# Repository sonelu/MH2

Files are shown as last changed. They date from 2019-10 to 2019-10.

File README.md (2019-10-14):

# MH2

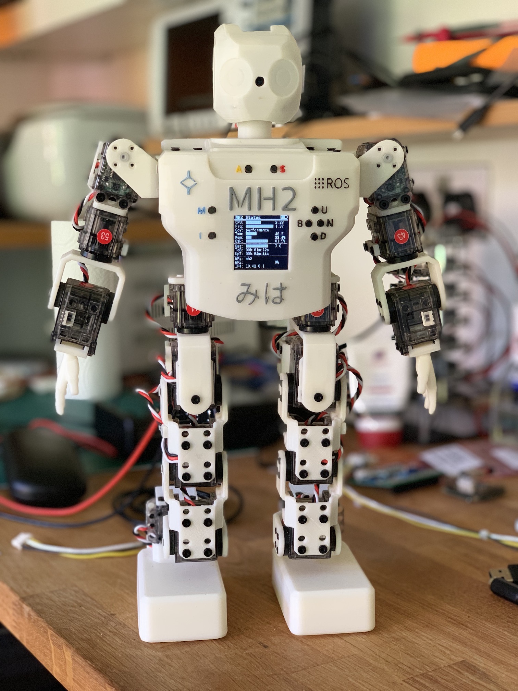
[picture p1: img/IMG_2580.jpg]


Miha 2 (Mini Humanoid Gen 2) is a 22 Degrees of Freedom (DOF) Humanoid Robot intended for research and learning.

The main features of the robot are:

* 22 high performance daisy chained actuators [XL-320](http://emanual.robotis.com/docs/en/dxl/x/xl320/) from Robotis
* Main controller: [FriendlyElec NanoPi Neo Core2 LTS](https://www.friendlyarm.com/index.php?route=product/product&path=69&product_id=211) with:
  - Quad-Core Allwinner H5 processor at 1.5GHz
  - 1GB RAM
  - only 7g weight
* [Custom add-on board](add-on.md) with:
  - 4 channels Dynamixel bus (provided by a [FTDI4232H](https://www.ftdichip.com/Support/Documents/DataSheets/Modules/DS_FT4232H_Mini_Module.pdf) (USB to UART 4 channels)
  - [LSM330](https://media.digikey.com/pdf/Data%20Sheets/ST%20Microelectronics%20PDFS/LSM330.pdf) 6 axis IMU (accelerometer and gyroscope)
  - [Murata 5V 1.5A high performance DC/DC convertor](https://power.murata.com/data/power/oki-78sr.pdf)
* 5MP USB camera (in the head)
* 1.5" 128x128 pixel OLED display (I2C SSD1327 chip)
* 8 tactile switches controlled with a TCA9538 I2C I/O expander providing easy interation with the menues on display
* Power provided by 4 18650 industry standard rechargeable batteries located in the feet and hotswappable; the hotswap capability is provided by a pair of small cicuits that provide a "smart diode" functionality, preventing rush current while chainging the batteries. **A full charge allows aproximatelly 4 hours of operation**.

The [software](./mh2/) is based on the [pypot](https://github.com/poppy-project/pypot) library and I have plans to include ROS support by leveraging the [ROBOTIS-Framework](https://github.com/ROBOTIS-GIT/ROBOTIS-Framework) packages.

The [robot parts](./stl) are 3D printed.

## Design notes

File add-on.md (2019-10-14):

# Add-On Board for MH2

The MH2 robot uses the [FriendlyElec NanoPi Neo Core2 LTS](https://www.friendlyarm.com/index.php?route=product/product&path=69&product_id=211) main controller. To control the Dynamixel servomotors it uses a custom add-on board:

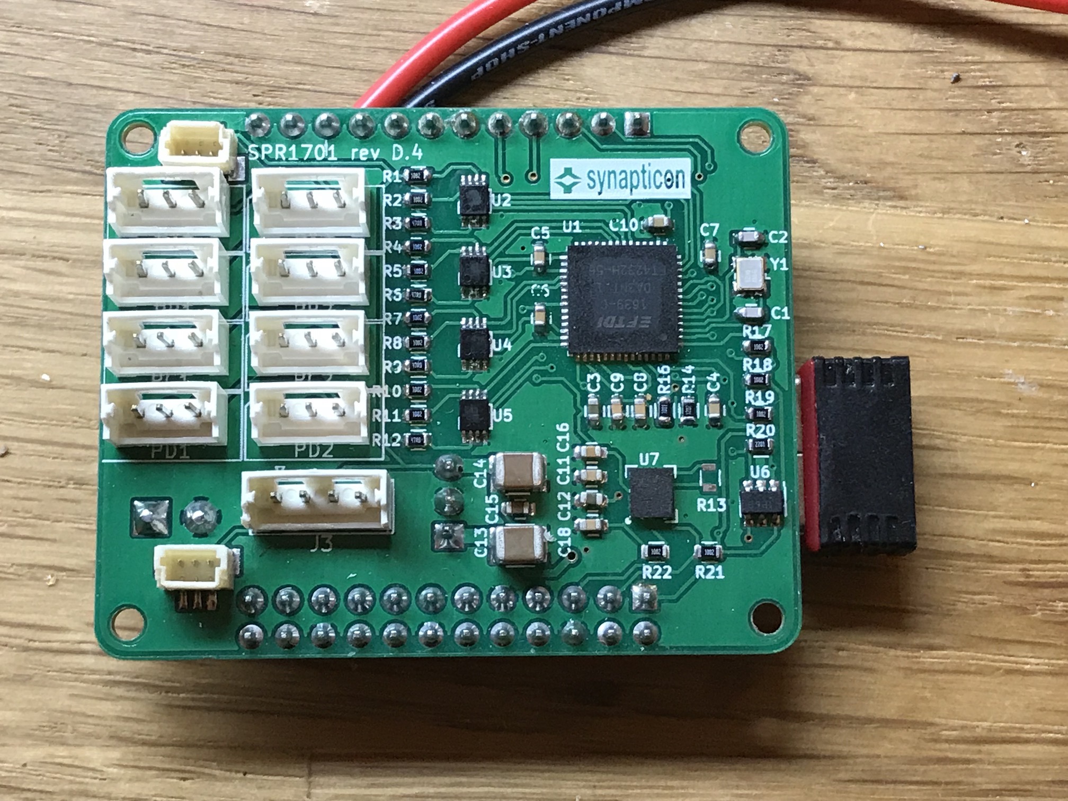
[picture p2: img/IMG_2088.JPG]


This board provides the following:

* uses one of the USB from the NanoPi board and [FTDI4232H](https://www.ftdichip.com/Support/Documents/DataSheets/ICs/DS_FT4232H.pdf) chip to produce 4 UART channels (they will appear as /dev/ttyUSB0 to /dev/ttyUSB3 to the operating system)
* the FTDI chip is programmed using a [93LC46BT](http://www.microchip.com/mymicrochip/filehandler.aspx?ddocname=en550232) 1K EEPROM to configure it in RS485 mode (see page 20 in the FTDI4232 datasheet); this way we can easily convert the RX/TX dignals from the UARTs in a semi-duplex signal required by the Dynamixel bus
* the RX/TX pairs and TXDEN is then passed through a [74LVC2G241](http://www.ti.com/general/docs/suppproductinfo.tsp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) buffer for each of the 4 UARTs, producing the 1 wire [semi-duplex](http://emanual.robotis.com/docs/en/dxl/x/xl320/#communication-circuit) serial signal used by the Dynamixel servos
* there are 8 Dynamixel XL-320 connectors ([Molex 53253-0370](https://www.molex.com/molex/products/datasheet.jsp?part=active/0532530370_PCB_HEADERS.xml)), 2 for each channel
* connected on the I2C there is a [LSM330](https://media.digikey.com/pdf/Data%20Sheets/ST%20Microelectronics%20PDFS/LSM330.pdf) 6 axis IMU (accelerometer and gyroscope) that the robot can use to evaluate the posture
* a 4 pin Molex connector for I2C (used by the OLED screen and the button I/O expander)
* 2 connectors for the cooling fans

On the back side of the board we have:

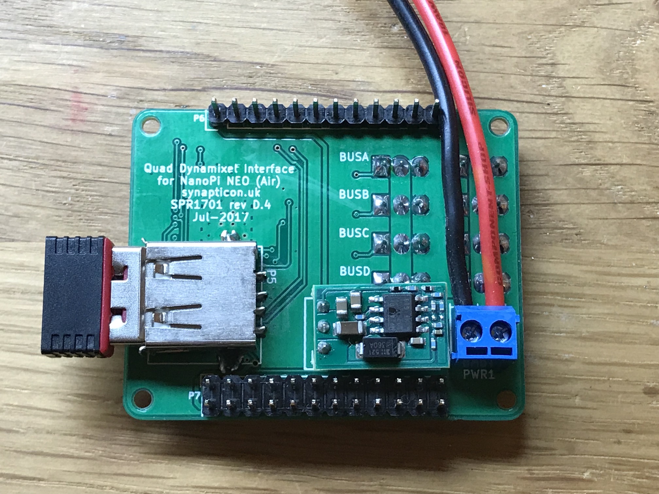
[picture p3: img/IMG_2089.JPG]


* one USB connector for the WiFi dongle (the board does not have WiFi onboard)
* the 5V regulator (1.5A) [Murata OKI-78SR-5/1.5-W36-C](https://power.murata.com/data/power/oki-78sr.pdf)
* the connector the external power jack

The board is fitted directly on top of the GPIO pins of the NanoPi Neo Core2 board:

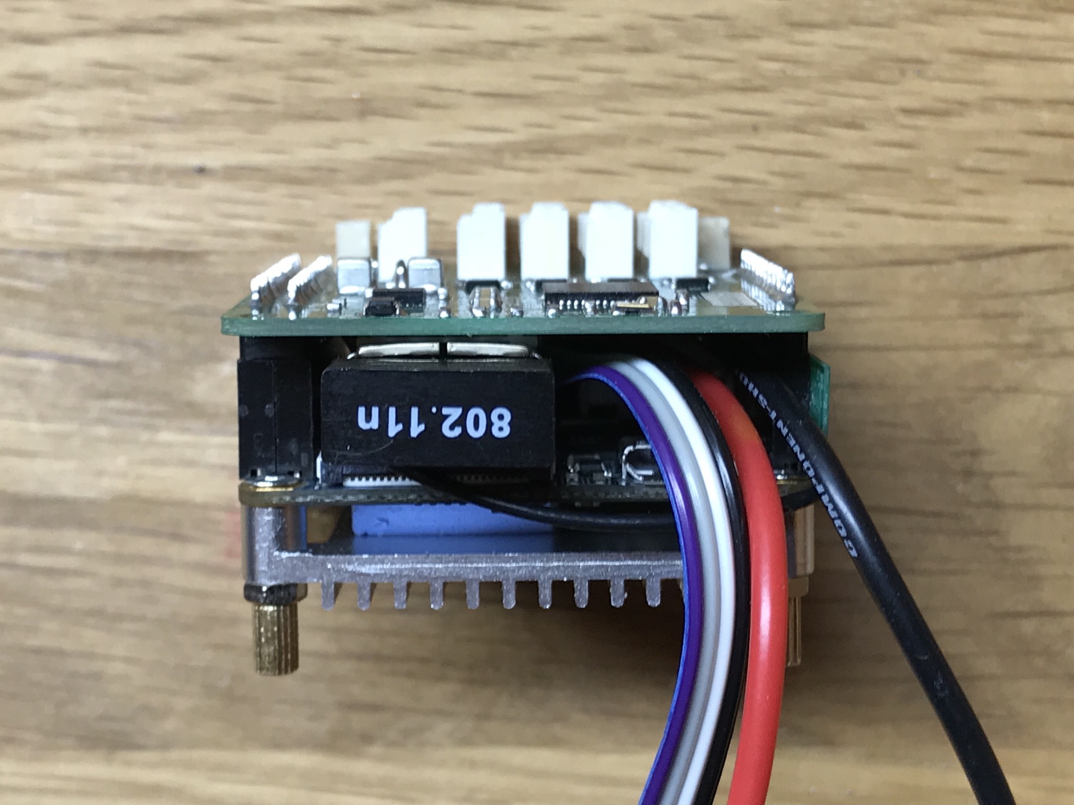
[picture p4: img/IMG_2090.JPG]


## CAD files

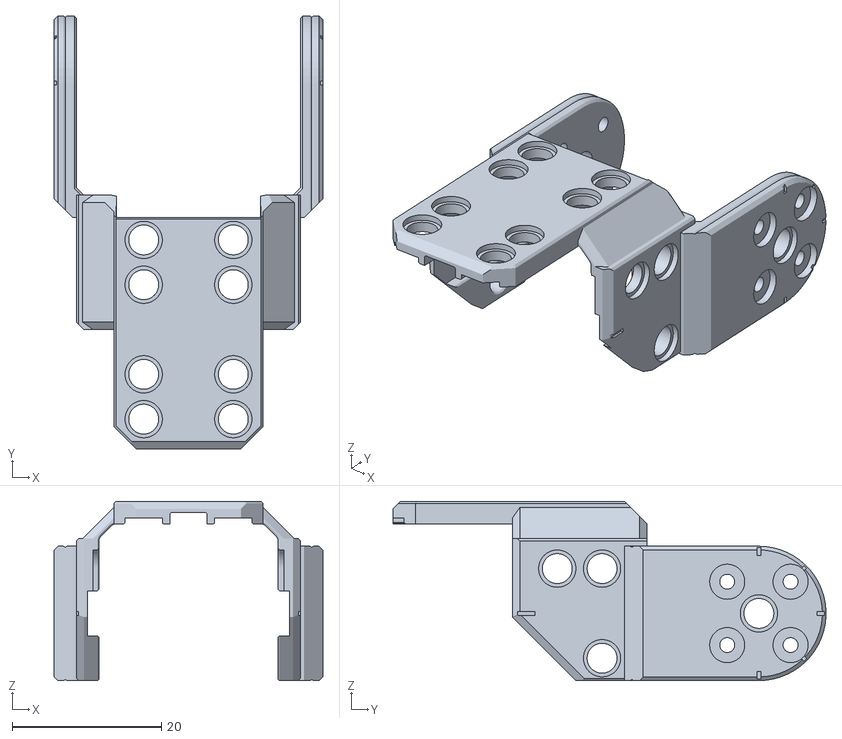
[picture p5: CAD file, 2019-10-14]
stl/MH2-22 - simpler hip.stl
36.0 x 58.0 x 24.0

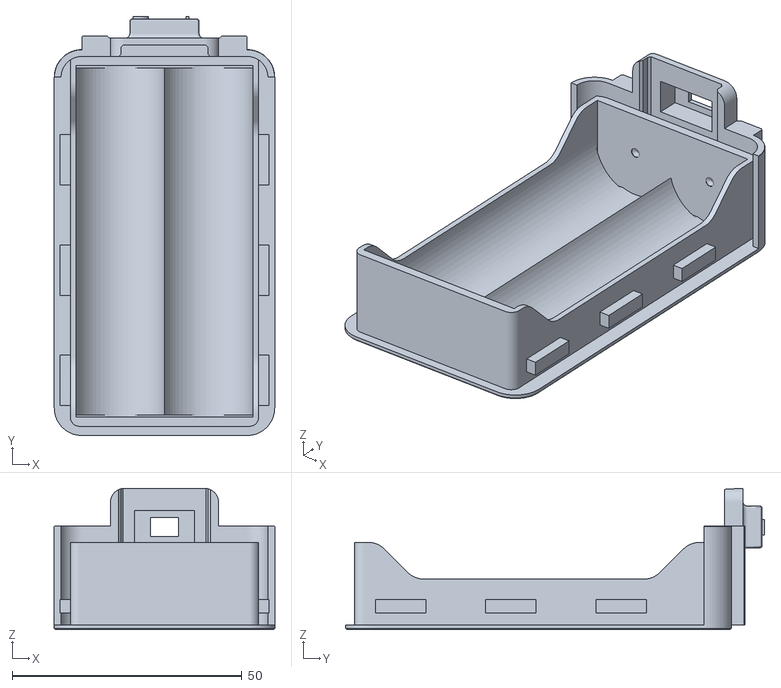
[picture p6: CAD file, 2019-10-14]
stl/MH2-22 - sole.stl
48.0 x 91.2 x 30.8

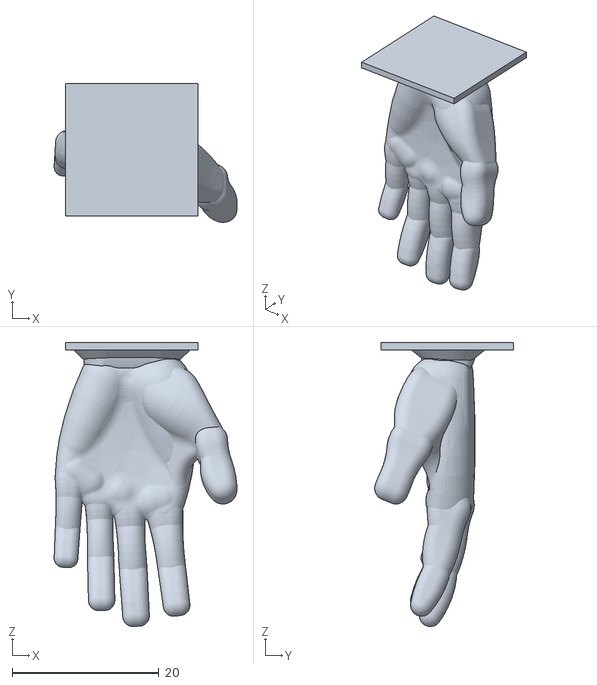
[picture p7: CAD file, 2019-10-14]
stl/MH2-22 - left hand.stl
24.9 x 18.9 x 38.6

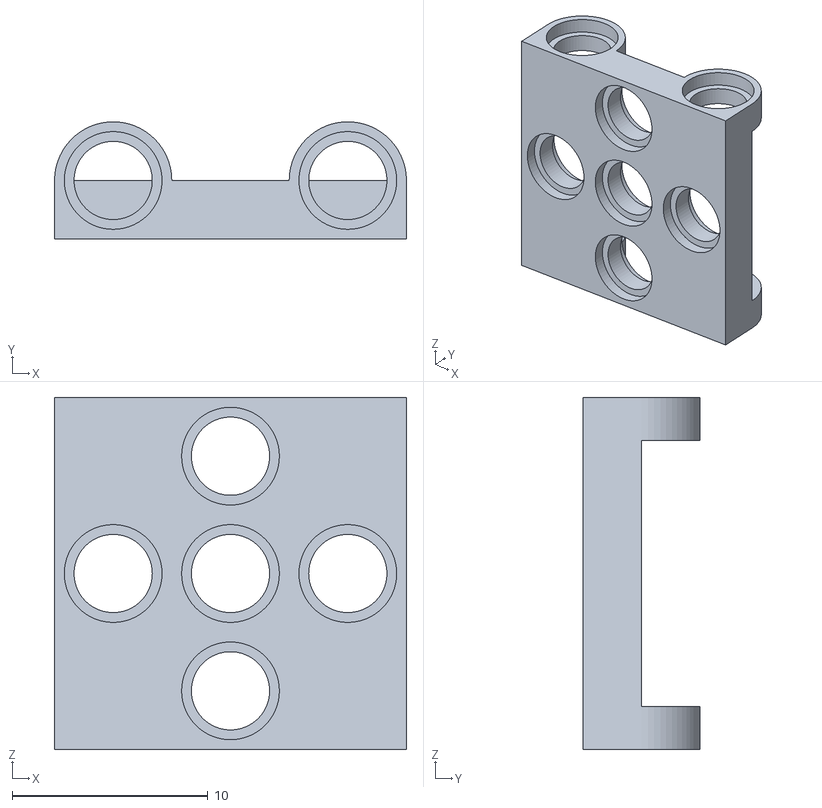
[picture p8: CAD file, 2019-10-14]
stl/MH2-22 - SPU-5(W).stl
18.0 x 6.00 x 18.0

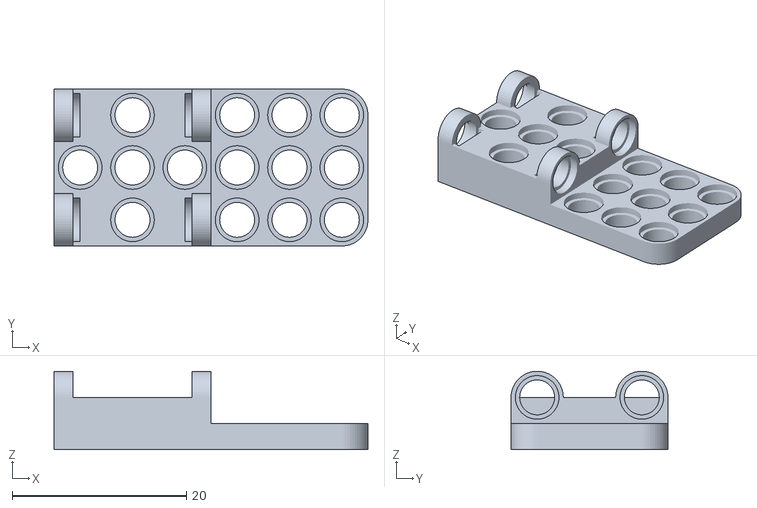
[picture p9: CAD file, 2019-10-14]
stl/MH2-22 - SPU-5-combo.stl
36.0 x 18.0 x 9.00

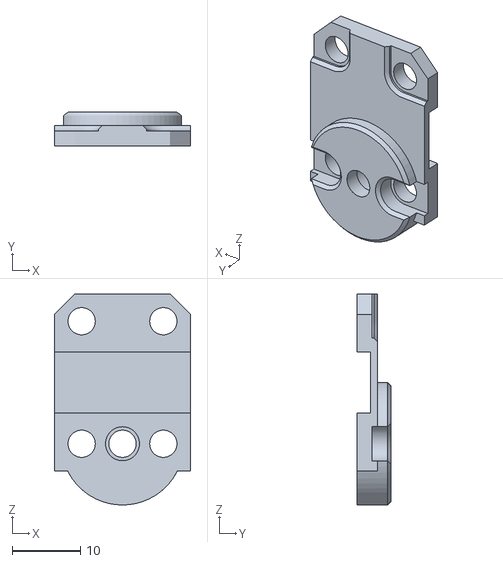
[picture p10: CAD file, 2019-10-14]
stl/MH2-22 - hip idle.stl
20.0 x 5.00 x 31.0

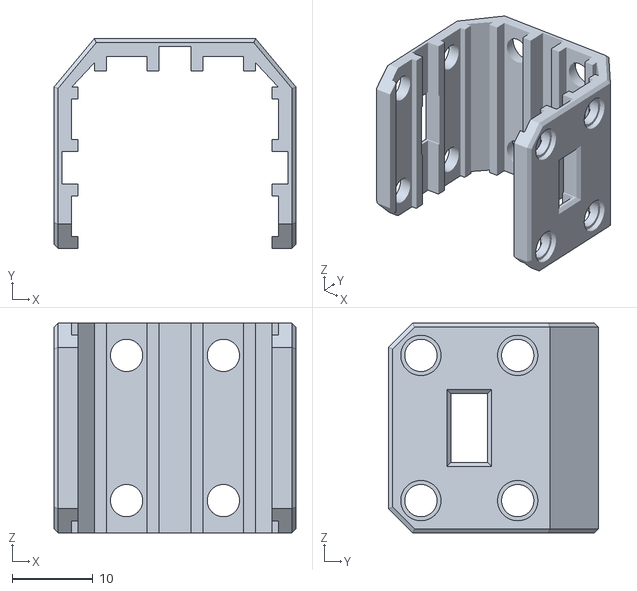
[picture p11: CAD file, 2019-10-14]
stl/MH2-22 - hip connector.stl
30.0 x 26.0 x 26.0

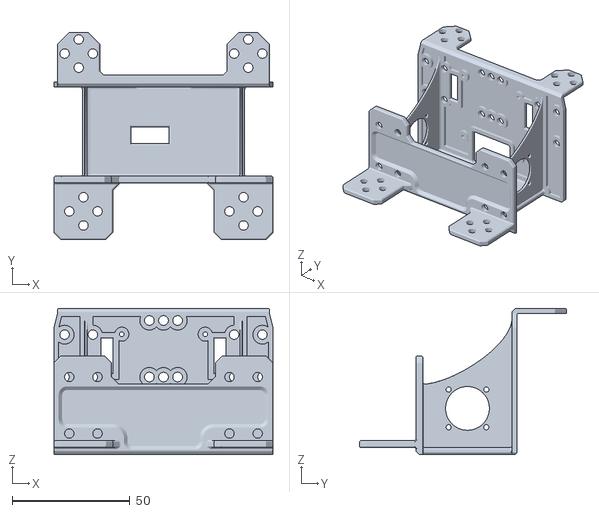
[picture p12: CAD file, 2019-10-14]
stl/MH2-22 - chest.stl
93.0 x 88.0 x 62.2

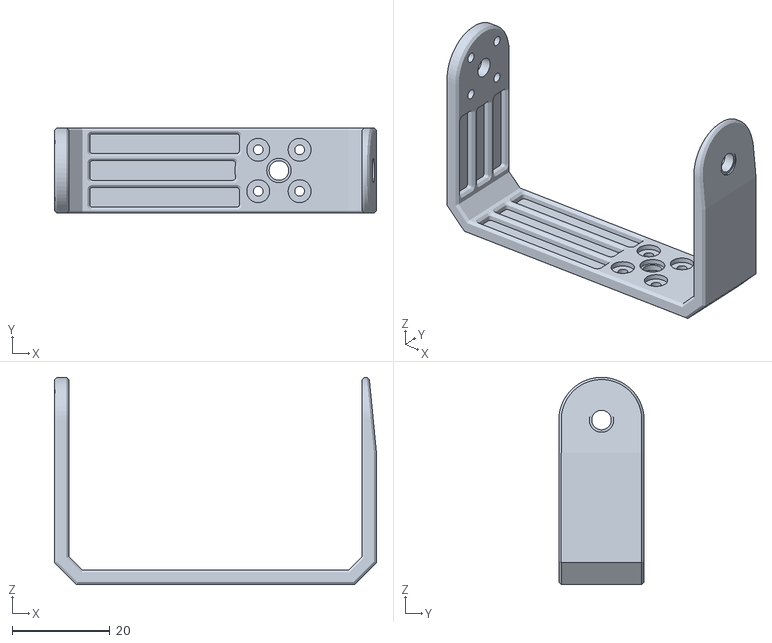
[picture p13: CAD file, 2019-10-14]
stl/MH2-22 - long U.stl
66.0 x 17.5 x 42.5

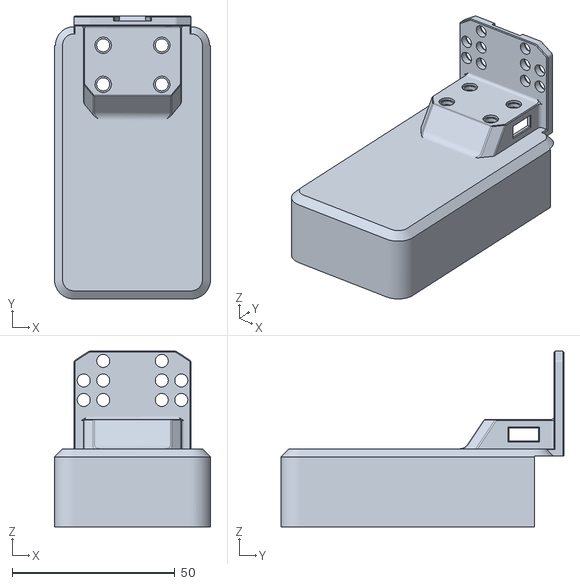
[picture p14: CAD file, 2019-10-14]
stl/MH2-22 - foot.stl
48.0 x 87.0 x 54.0

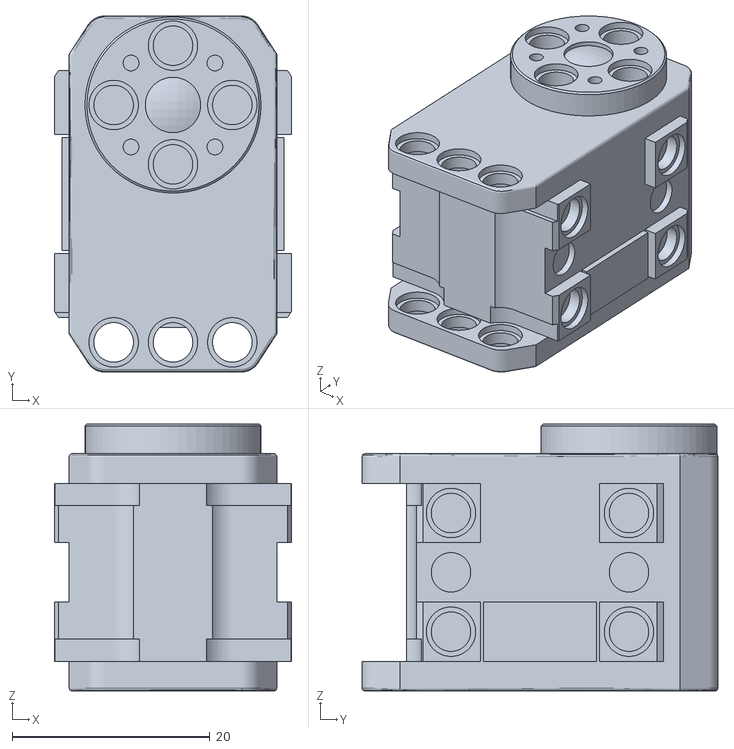
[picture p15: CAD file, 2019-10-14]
stl/MH2-22 - XL-320.stl
24.0 x 36.0 x 27.0

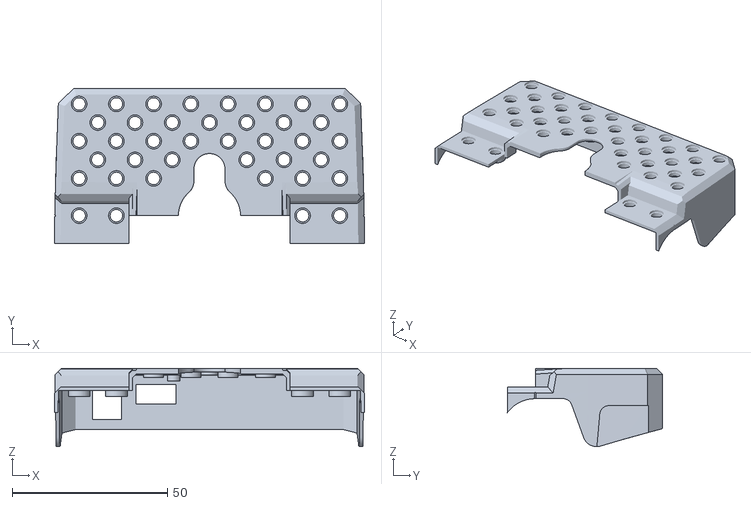
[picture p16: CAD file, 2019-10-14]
stl/MH2-22 - skin back (wide).stl
99.9 x 50.0 x 25.2

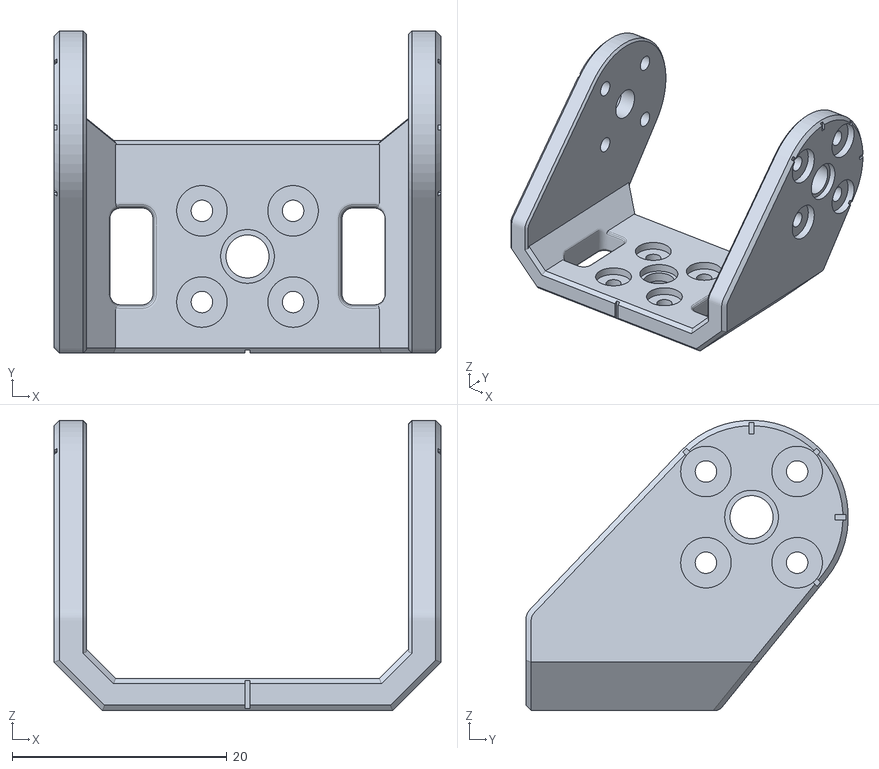
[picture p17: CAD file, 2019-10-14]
stl/MH2-22 - shoulder.stl
36.0 x 30.0 x 27.0

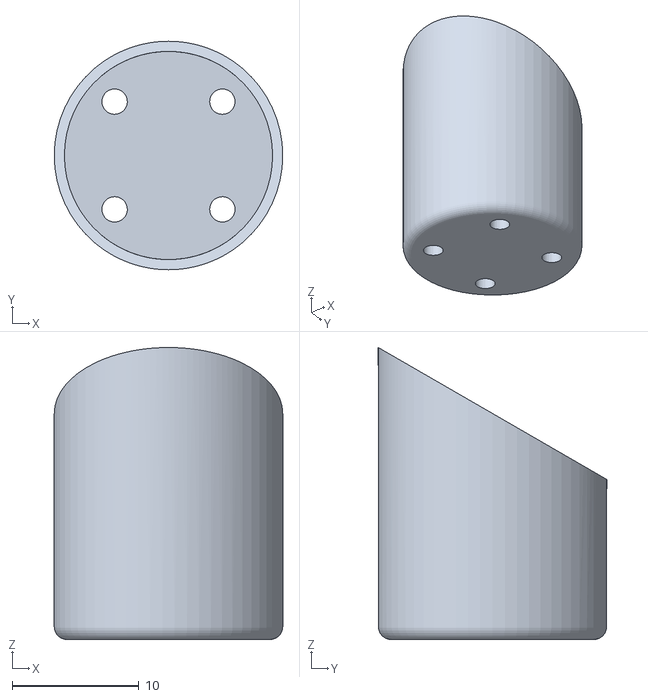
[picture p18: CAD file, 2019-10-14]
stl/MH2-22 - neck.stl
18.0 x 18.0 x 23.0

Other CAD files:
stl/MH2-22 - right hand.stl
stl/MH2-22 - 18mm cable tidy.stl
stl/MH2-22 - straight U.stl
stl/MH2-22 - SPO-5(GR).stl
stl/MH2-22 - 12mm cable tidy.stl
stl/MH2-22 - hand base.stl
stl/MH2-22 - head support.stl
stl/MH2-22 - head.stl
stl/MH2-22 - skin front.stl

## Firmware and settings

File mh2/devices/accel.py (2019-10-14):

import smbus2
import time


class LSM330():

    def __init__(self, busno=0, addr_g=0x6a, addr_a=0x1e):
        self.busno = busno
        self.addr_g = addr_g
        self.addr_a = addr_a 

        self.bus = smbus2.SMBus(self.busno)
        # configure gyro
        # 0x20h is the control register
        # 0x0f is all axes ON and default 95Hz DR and 12.5Hz BW (see page 60 in manual)
        self.bus.write_byte_data(self.addr_g, 0x20, 0x0F)

        # configure accelerometer
        # 0x20 is the control register
        # 0x67 is 100Hz all axes on
        self.bus.write_byte_data(self.addr_a, 0x20, 0x67)
        time.sleep(0.5)

    def __read2bytes(self, dev_addr, reg_addr):
        d0 = self.bus.read_byte_data(dev_addr, reg_addr)
        d1 = self.bus.read_byte_data(dev_addr, reg_addr+1)
        val = d1 * 256 + d0
        if val > 32767:
            val -= 65536
        return val

    def get_acc(self):
        x_a = self.__read2bytes(self.addr_a, 0x28)
        y_a = self.__read2bytes(self.addr_a, 0x2A)
        z_a = self.__read2bytes(self.addr_a, 0x2C)
        return (x_a, y_a, z_a)

    def get_gyro(self):
        x_g = self.__read2bytes(self.addr_g, 0x28)
        y_g = self.__read2bytes(self.addr_g, 0x2A)
        z_g = self.__read2bytes(self.addr_g, 0x2C)
        return (x_g, y_g, z_g)

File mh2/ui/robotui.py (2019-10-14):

import smbus2

from screenloop import UIScreenLoop

import time
import subprocess


class RobotUI():                                         

    def __init__(self, robot):
        self.robot = robot
        self.bus = smbus2.SMBus(0)
        self.bus.write_byte_data(0x70, 0x03, 0xff)
        self.lastbutt = 255          

    def processKeys(self):
        butt = self.bus.read_byte_data(0x70, 0x00)
        if butt != self.lastbutt:
            display = self.robot.screen_loop
            navigation = display.navigation()
            if butt == 247 and 'I' in navigation:
                # info button
                display.switchScreen(navigation['I'])
            elif butt == 253 and 'M' in navigation:
                # menu button 
                display.switchScreen(navigation['M'])
            elif butt == 127 and 'U' in navigation and navigation['U'] == True:
                # button up
                display.navUp()
            elif butt == 239 and 'D' in navigation and navigation['D'] == True:
                # button down
                display.navDown()
            elif butt == 191 and 'B' in navigation:
                # back button
                display.switchScreen(navigation['B'])
            elif butt == 223 and 'F' in navigation:
                # forward button
                sel = display.screen.cursel
                if navigation['F'][sel] == "__action__":
                    getattr(self, display.screen.actions[sel])()
                else:
                    display.switchScreen(navigation['F'][sel])
            elif butt == 254:
                if 'S' in navigation:
                    display.switchScreen(navigation['S']) 
                else:
                    display.switchScreen('shutDown') 

            self.lastbutt = butt

    def stopRobot(self):
        display = self.robot.screen_loop
        display.switchScreen('info')
        display.screen.title = "Stopping Robot"
        self.commonStop()

    def powerDown(self):
        subprocess.check_output('sudo shutdown -h', shell=True)
        display = self.robot.screen_loop
        display.switchScreen('info')
        display.screen.title = "Power Down"
        display.screen.updateText("Shutdown Requested.\nWill power off\nin 1min")
        time.sleep(2)
        self.commonStop()

    def resetSoC(self):
        subprocess.check_output('sudo shutdown -r', shell=True)
        display = self.robot.screen_loop
        display.switchScreen('info')
        display.screen.title = "Reboot"
        display.screen.updateText("Reboot Requested.\nWill reboot\nin 1min")
        time.sleep(2)
        self.commonStop()

    def commonStop(self):
        screen = self.robot.screen_loop.screen
        for count in range(5,0, -1):
            screen.updateText("Robot will\nbecome compliant\nin {}s".format(count))
            time.sleep(1)
        screen.updateText("Making\ncompliant...")
        self.robot.compliant = True
        screen.updateText("Closing down\nrobot...")
        self.robot.close()
        screen.updateText("Finished.\nBye")
        #sys.exit() # we need to close this thread too

    def toggleMove(self, title, text, primitive, sleep):
        display = self.robot.screen_loop
        old_screen = display.switchScreen('info')
        display.screen.title = title
        display.screen.text = text
        if primitive.is_alive():
            primitive.stop()
        else:
            primitive.start()
        time.sleep(sleep)
        display.switchScreen(old_screen)

    def startStandUp(self):
        self.toggleMove("Stand Up", "Running\nStand Up\nMove", self.robot.stand_position, 2)

    def startSitDown(self):
        self.toggleMove("Sit Down", "Running\nSit Down\nMove", self.robot.sit_position, 2)

    def startHeadIdle(self):
        self.toggleMove("Head Idle", "Toggling\nHead Idle\nMove", self.robot.head_idle_motion, 2)

    def startWaveLeft(self):
        self.toggleMove("Wave Left", "Running\nWave Left\nMove", self.robot.wave_left, 2)
        
    def startWaveBoth(self):
        self.toggleMove("Wave Both", "Running\nWave Both\nMove", self.robot.wave_both, 2)

    def turnCompliantOn(self): 
        self.robot.compliant = True
        self.robot.screen_loop.splashScreen('Compliant On', 'Turned\nCompliant\nON', 2)

    def turnCompliantOff(self): 
        self.robot.power_up()
        self.robot.screen_loop.splashScreen('Compliant Off', 'Turned\nCompliant\nOFF', 2)

    def turnHandsCompliant(self):
        self.robot.turnHandsCompliant()
        self.robot.screen_loop.splashScreen('Hands', 'Turned\nHands\nCompliant', 2)

    def turnLegsCompliant(self):
        self.robot.turnLegsCompliant()
        self.robot.screen_loop.splashScreen('Legs', 'Turned\nLegs\nCompliant', 2)

    def turnHeadCompliant(self):
        self.robot.turnHeadCompliant()
        self.robot.screen_loop.splashScreen('Legs', 'Turned\nHead\nCompliant', 2)


    def governorPerformance(self): self.robot.changeGovernor('performance')
    def governorOnDemand(self): self.robot.changeGovernor('ondemand')
    def governorPowerSave(self): self.robot.changeGovernor('powersave')
    def governorConservative(self): self.robot.changeGovernor('conservative')
